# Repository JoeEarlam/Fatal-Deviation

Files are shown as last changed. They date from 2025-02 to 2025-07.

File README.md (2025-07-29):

# Fatal Deviation

Fatal Deviation is my 1.5KG beetleweight lifter, with independent 4WD and electronic stability control. The name comes from Ireland's first full-length martial arts movie of the same name, which can be found in its entirety on youtube for the morbidly curious.

This repository is not intended to be instructional - this isn't a full open-source project, but a reference for myself and others who want to see how the sausage is made. If you do build your own (or something similar), please let me know, I'd love to see more weird tiny beetleweights on the scene!

For more information on the design and build process, please check out my build thread: https://forum.bristolbotbuilders.com/t/fatal-deviation-my-over-engineered-beetleweight/232

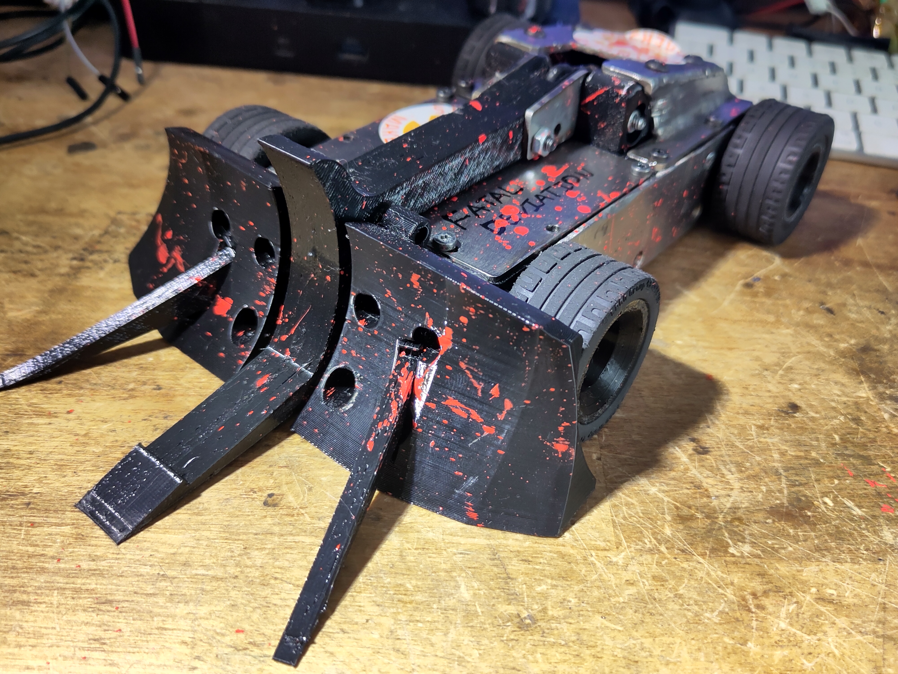
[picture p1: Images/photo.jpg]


TPU front end, the night before Bristol Bot Builders' Summer Showdown, July 2025



Steel front end, for Robodojo, May 2025

## Design Criteria and Overview

I impulse bought a TIG welder in Lidl and needed more excuses to use it. Somebody on the internet said that it wasn't possible to build a somewhat competitive beetleweight robot almost entirely from steel. Together, that was all the motivation I needed. Watching fast lifter/grappler bots like P1, Whiplash, Claw Viper/Red Storm, and having previous experience racing RC cars, I knew how I wanted the bot to drive - fast, agile, predictable. This gave me some design requirements:

* Extremely compact chassis to allow as much armour coverage as possible.
* Four independently controlled drive motors, for redundancy and torque vectoring.
* Small, compact and powerful lifter mechanism.
* As much RGB as possible while still having enough power left over for the bot to drive.

## Mechanical Design

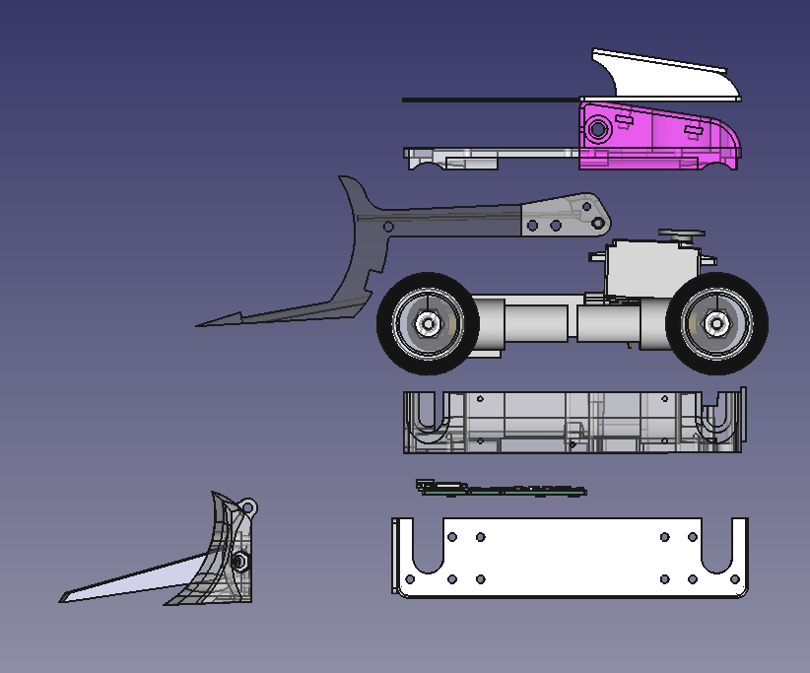
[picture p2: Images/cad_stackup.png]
CAD stackup


The mechanical design uses a welded 304 stainless steel chassis tub - 2mm sides and bottom, with 4mm front and rear sections. Stainless was chosen for aesthetic reasons, and because 2mm hardox is very difficult to source.

The wedge is soft-mounted via threaded aluminium inserts pressed into TPU brackets. The tub protects a TPU clamshell that sandwiches the internal components together, via long screws and threaded inserts to pull it together. Self-tapping screws are used to hold the clamshell into the chassis tub which suspends all the internal components and hopefully provides some shock absorption.

The TPU clamshell design means all the internal components of the robot can be removed as a unit for repair on the bench. Accessing any component only takes a couple of minutes, although unfortunately due to the compact design many connections have to be soldered rather than connectorised/

## Electronic Design

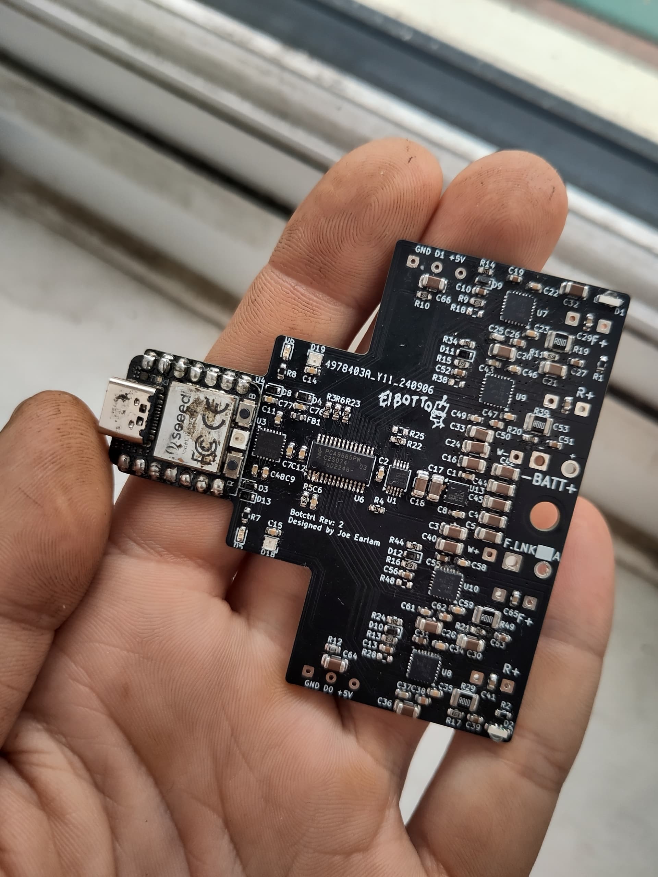
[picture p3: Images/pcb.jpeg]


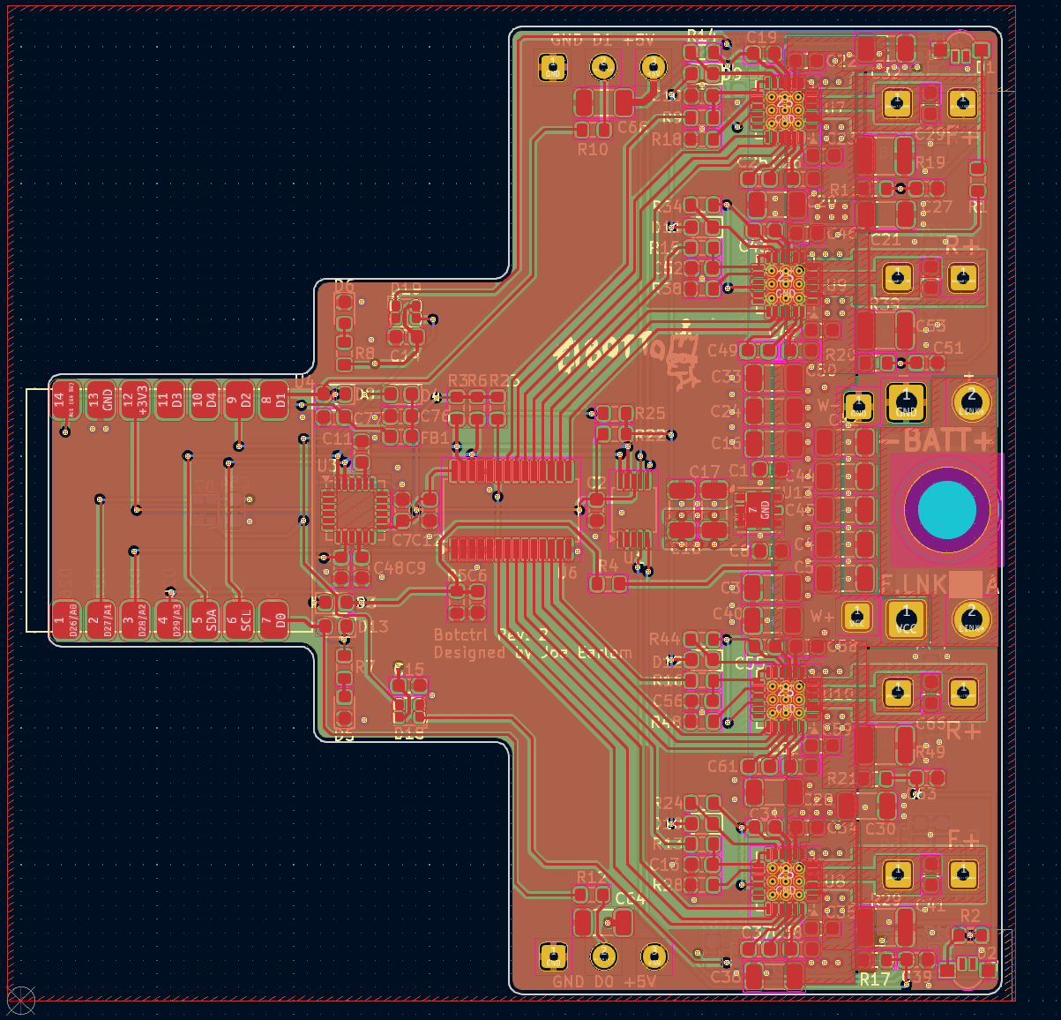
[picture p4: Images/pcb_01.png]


The only way to cram electronics into the remaining space inside the bot is to integrate every function (aside from the receiver) into a single PCB. In approximately 50x70mm total board area, the PCB provides:

* Seeed Xiao RP2040 microcontroller
* 4x 6A drive channels (TI DRV8256P drivers), with current sensing.
* MPU6050 gyro + accelerometer
* IBUS receiver compatible
* Servo power and signal pads
* 7x WS2812 RGB LEDs

The four layer PCB was designed with heavy usage of copper pours, optimised to keep resistance (both electrical and thermal) and inductance as low as possible when using cheap 1oz copper fabrication processes (2oz often costs 3-4 as much as 1oz!). The design also keeps the hot and EMI-prone motor drivers and servo power pads far away from the sensitive IMU and MCU. While only supposed to run 2-3 minutes at a time for events, it's been stress tested with 5-10 minutes of continuous running and barely rises over 45c, even with no airflow and four hot motors spinning inside the bot.

## Software Design

The software is written in Arduino IDE, utilising both cores of the RP2040 microcontroller. The firmware uses the wonderful [TaskScheduler](https://github.com/arkhipenko/TaskScheduler) library by arkhipenko to handle timing and looping, with modularity provided by custom classes containing motor driver logic, IMU data processing, and drive maths. The task-based asynchronous code allows predictable timing for data acquisition and filter functions, while also optimising for minimum latency by triggering drive maths routines the instant that a new radio packet is received.

IMU gyroscope data is used, in combination with the steering channel data received from the RC transmitter, as the input and target variables of a PID loop, which provides the electronic stability control - the bot will steer to self correct back to its intended course if disrupted; either by a bump in the floor or contact with another robot, and allows the bot to hold dead straight line acceleration or smooth drifts on low-friction surfaces where it would otherwise spin out uncontrollably. To improve the turning radius (which is otherwise somewhat poor due to the long aspect ratio of the bot) the front inside wheel is braked on sharp turns, while the rear inside wheel coasts, shifting the centre of rotation for the bot forwards.

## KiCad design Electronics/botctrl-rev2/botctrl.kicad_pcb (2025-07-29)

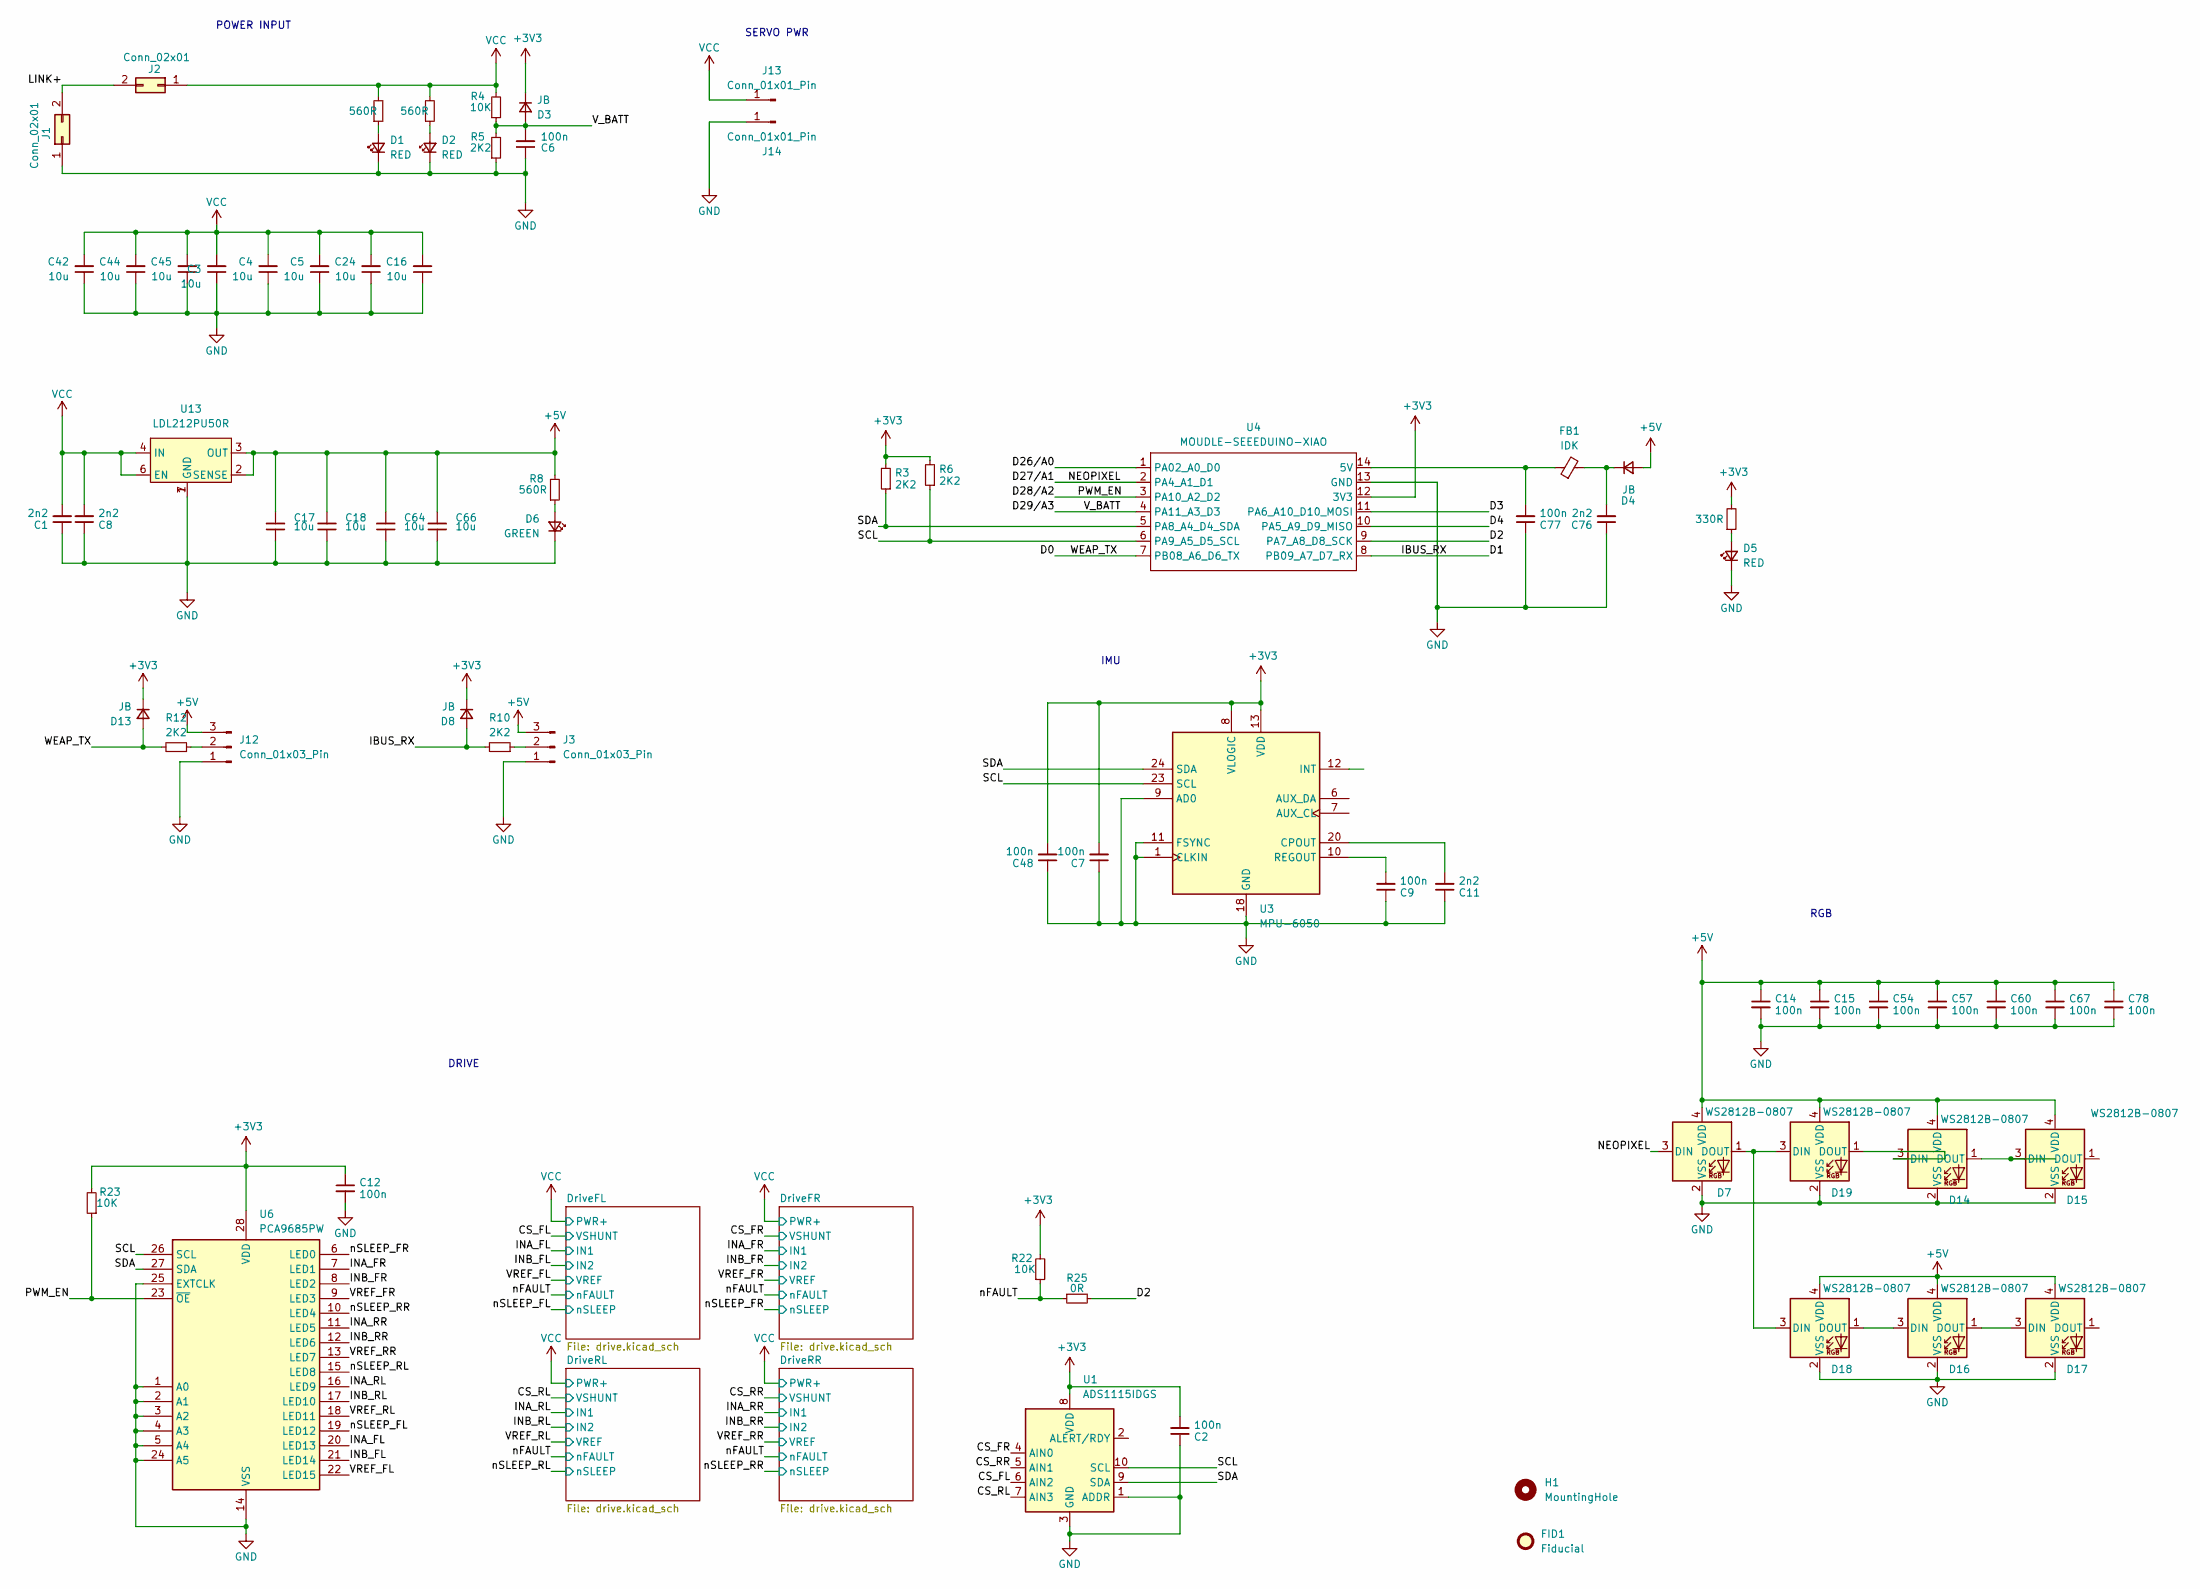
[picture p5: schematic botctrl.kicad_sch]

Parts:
C1, C8, C11, C76: 2n2; C_0603_1608Metric
C2, C6, C7, C9, C12, C14, C15, C48, C54, C57, C60, C67, C77, C78: 100n; C_0603_1608Metric
C3, C4, C5, C16, C17, C18, C24, C42, C44, C45, C64, C66: 10u; C_1206_3216Metric
D1, D2: RED; LED_Kingbright_APFA3010_3x1.5mm_Horizontal
D3, D4, D8, D13: JB; D_0603_1608Metric
D5: RED; D_0603_1608Metric
D6: GREEN; D_0603_1608Metric
D7, D14, D15, D16, D17, D18, D19: WS2812B-0807; WS2812-0807
FB1: IDK; L_0603_1608Metric; Part Number 0R
FID1: Fiducial; el-botto
H1: MountingHole; MountingHole_4.3mm_M4_DIN965
J1, J2: Conn_02x01; SolderWire-0.75sqmm_1x02_P4.8mm_D1.25mm_OD2.3mm
J3, J12: Conn_01x03_Pin; SolderWire-0.127sqmm_1x03_P3.7mm_D0.48mm_OD1mm
J13, J14: Conn_01x01_Pin; SolderWire-0.25sqmm_1x01_D0.65mm_OD1.7mm
R1, R2, R8: 560R; R_0603_1608Metric
R3, R5, R6, R10, R12: 2K2; R_0603_1608Metric
R4, R22, R23: 10K; R_0603_1608Metric
R7: 330R; R_0603_1608Metric
R25: 0R; R_0603_1608Metric
U1: ADS1115IDGS; TSSOP-10_3x3mm_P0.5mm
U3: MPU-6050; InvenSense_QFN-24_4x4mm_P0.5mm
U4: MOUDLE-SEEEDUINO-XIAO; MOUDLE14P-SMD-2.54-21X17.8MM
U6: PCA9685PW; TSSOP-28_4.4x9.7mm_P0.65mm
U13: LDL212PU50R; DFN-6-1EP_3x3mm_P0.95mm_EP1.7x2.6mm

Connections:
+3V3: C2.2, C7.2, C12.1, C48.2, D3.1 (K), D8.1 (K), D13.1 (K), R3.2, R6.2, R7.2, R22.2, R23.2, U1.8 (VDD), U3.8 (VLOGIC), U3.13 (VDD), U4.12 (3V3), U6.28 (VDD)
+5V: C14.1, C15.1, C17.2, C18.2, C54.1, C57.1, C60.1, C64.2, C66.2, C67.1, C78.1, D4.2 (A), D7.4 (VDD), D14.4 (VDD), D15.4 (VDD), D16.4 (VDD), D17.4 (VDD), D18.4 (VDD), D19.4 (VDD), J3.3, J12.3, R8.2, U13.2 (SENSE), U13.3 (OUT)
/CS_FL: U1.6 (AIN2); also elsewhere on the board
/CS_FR: U1.4 (AIN0); also elsewhere on the board
/CS_RL: U1.7 (AIN3); also elsewhere on the board
/CS_RR: U1.5 (AIN1); also elsewhere on the board
/D0: D13.2 (A), R12.2, U4.7 (PB08_A6_D6_TX)
/D1: D8.2 (A), R10.2, U4.8 (PB09_A7_D7_RX)
/D2: R25.2, U4.9 (PA7_A8_D8_SCK)
/D3: U4.11 (PA6_A10_D10_MOSI)
/D4: U4.10 (PA5_A9_D9_MISO)
/D26/A0: U4.1 (PA02_A0_D0)
/D27/A1: D7.3 (DIN), U4.2 (PA4_A1_D1)
/D28/A2: R23.1, U4.3 (PA10_A2_D2), U6.23 (~OE)
/D29/A3: C6.2, D3.2 (A), R4.1, R5.2, U4.4 (PA11_A3_D3)
/INA_FL: U6.20 (LED13); also elsewhere on the board
/INA_FR: U6.7 (LED1); also elsewhere on the board
/INA_RL: U6.16 (LED9); also elsewhere on the board
/INA_RR: U6.11 (LED5); also elsewhere on the board
/INB_FL: U6.21 (LED14); also elsewhere on the board
/INB_FR: U6.8 (LED2); also elsewhere on the board
/INB_RL: U6.17 (LED10); also elsewhere on the board
/INB_RR: U6.12 (LED6); also elsewhere on the board
/LINK+: J1.2, J2.2
/SCL: R6.1, U1.10 (SCL), U3.23 (SCL), U4.6 (PA9_A5_D5_SCL), U6.26 (SCL)
/SDA: R3.1, U1.9 (SDA), U3.24 (SDA), U4.5 (PA8_A4_D4_SDA), U6.27 (SDA)
/VREF_FL: U6.22 (LED15); also elsewhere on the board
/VREF_FR: U6.9 (LED3); also elsewhere on the board
/VREF_RL: U6.18 (LED11); also elsewhere on the board
/VREF_RR: U6.13 (LED7); also elsewhere on the board
/nFAULT: R22.1, R25.1; also elsewhere on the board
/nSLEEP_FL: U6.19 (LED12); also elsewhere on the board
/nSLEEP_FR: U6.6 (LED0); also elsewhere on the board
/nSLEEP_RL: U6.15 (LED8); also elsewhere on the board
/nSLEEP_RR: U6.10 (LED4); also elsewhere on the board
GND: C1.1, C2.1, C3.1, C4.1, C5.1, C6.1, C7.1, C8.1, C9.1, C11.1, C12.2, C14.2, C15.2, C16.1, C17.1, C18.1, C24.1, C42.1, C44.1, C45.1, C48.1, C54.2, C57.2, C60.2, C64.1, C66.1, C67.2, C76.1, C77.1, C78.2, D1.1 (K), D2.1 (K), D5.1 (K), D6.1 (K), D7.2 (VSS), D14.2 (VSS), D15.2 (VSS), D16.2 (VSS), D17.2 (VSS), D18.2 (VSS), D19.2 (VSS), J1.1, J3.1, J12.1, J14.1, R5.1, U1.1 (ADDR), U1.3 (GND), U3.1 (CLKIN), U3.9 (AD0), U3.11 (FSYNC), U3.18 (GND), U4.13 (GND), U6.1 (A0), U6.2 (A1), U6.3 (A2), U6.4 (A3), U6.5 (A4), U6.14 (VSS), U6.24 (A5), U6.25 (EXTCLK), U13.1 (GND), U13.7 (GND); also elsewhere on the board
unnamed: D1.2 (A), R1.1
unnamed: D2.2 (A), R2.1
unnamed: C76.2, D4.1 (K), FB1.2
unnamed: D5.2 (A), R7.1
unnamed: D6.2 (A), R8.1
unnamed: D14.3 (DIN), D19.1 (DOUT)
unnamed: D14.1 (DOUT), D15.3 (DIN)
unnamed: D16.3 (DIN), D18.1 (DOUT)
unnamed: D16.1 (DOUT), D17.3 (DIN)
unnamed: D7.1 (DOUT), D18.3 (DIN), D19.3 (DIN)
unnamed: J3.2, R10.1
unnamed: J12.2, R12.1
unnamed: C11.2, U3.20 (CPOUT)
unnamed: C9.2, U3.10 (REGOUT)
unnamed: C77.2, FB1.1, U4.14 (5V)
VCC: C1.2, C3.2, C4.2, C5.2, C8.2, C16.2, C24.2, C42.2, C44.2, C45.2, J2.1, J13.1, R1.2, R2.2, R4.2, U13.4 (IN), U13.6 (EN); also elsewhere on the board

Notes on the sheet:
DRIVE
POWER INPUT
SERVO PWR
IMU
RGB

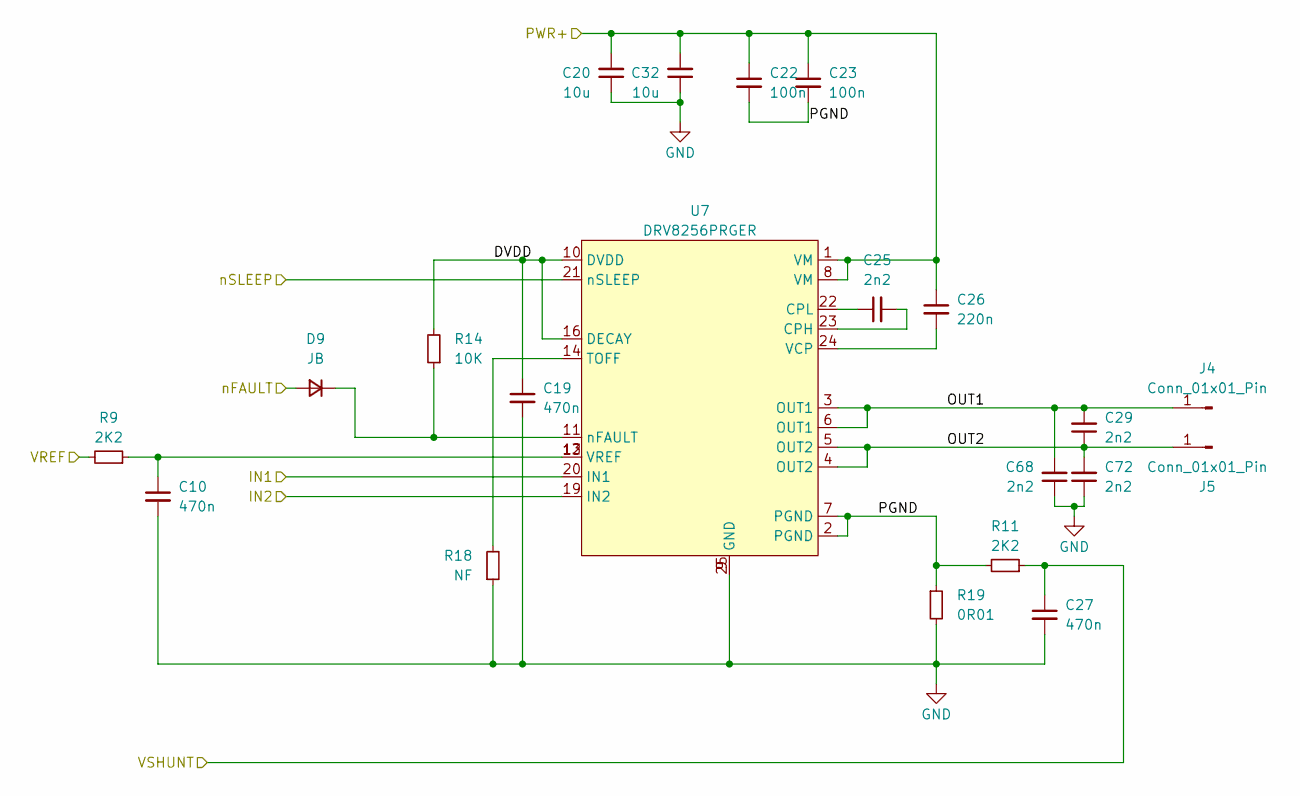
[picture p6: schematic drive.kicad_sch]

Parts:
C10, C19, C27: 470n; C_0603_1608Metric
C20, C32: 10u; C_1206_3216Metric
C22, C23: 100n; C_0603_1608Metric
C25, C29, C68, C72: 2n2; C_0603_1608Metric
C26: 220n; C_0603_1608Metric
D9: JB; D_0603_1608Metric
J4, J5: Conn_01x01_Pin; SolderWire-0.25sqmm_1x01_D0.65mm_OD1.7mm
R9, R11: 2K2; R_0603_1608Metric
R14: 10K; R_0603_1608Metric
R18: NF; R_0603_1608Metric
R19: 0R01; R_1210_3225Metric
U7: DRV8256PRGER; VQFN-24-1EP_4x4mm_P0.5mm_EP2.45x2.45mm_ThermalVias

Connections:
/CS_FL: C27.1, R11.1; also elsewhere on the board
/DriveFL/DVDD: C19.1, R14.2, U7.10 (DVDD), U7.16 (DECAY)
/DriveFL/OUT1: C29.2, C68.2, J4.1, U7.3 (OUT1), U7.6 (OUT1)
/DriveFL/OUT2: C29.1, C72.2, J5.1, U7.4 (OUT2), U7.5 (OUT2)
/DriveFL/PGND: C22.2, C23.2, R11.2, R19.1, U7.2 (PGND), U7.7 (PGND)
/INA_FL: U7.20 (IN1); also elsewhere on the board
/INB_FL: U7.19 (IN2); also elsewhere on the board
/VREF_FL: R9.2; also elsewhere on the board
/nFAULT: D9.2 (A); also elsewhere on the board
/nSLEEP_FL: U7.21 (nSLEEP); also elsewhere on the board
GND: C10.2, C19.2, C20.1, C27.2, C32.1, C68.1, C72.1, R18.1, R19.2, U7.9 (GND), U7.25 (GND); also elsewhere on the board
unnamed: C10.1, R9.1, U7.12 (VREF), U7.13 (VREF)
unnamed: D9.1 (K), R14.1, U7.11 (nFAULT)
unnamed: C25.2, U7.23 (CPH)
unnamed: C25.1, U7.22 (CPL)
unnamed: R18.2, U7.14 (TOFF)
unnamed: C26.2, U7.24 (VCP)
VCC: C20.2, C22.1, C23.1, C26.1, C32.2, U7.1 (VM), U7.8 (VM); also elsewhere on the board

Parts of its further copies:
C13, C31, C39, C43, C51, C52, C55, C56, C63: 470n; C_0603_1608Metric
C21, C28, C30, C33, C36, C40: 10u; C_1206_3216Metric
C34, C35, C46, C47, C58, C59: 100n; C_0603_1608Metric
C37, C41, C49, C53, C61, C65, C69, C70, C71, C73, C74, C75: 2n2; C_0603_1608Metric
C38, C50, C62: 220n; C_0603_1608Metric
D10, D11, D12: JB; D_0603_1608Metric
J6, J7, J8, J9, J10, J11: Conn_01x01_Pin; SolderWire-0.25sqmm_1x01_D0.65mm_OD1.7mm
R13, R15, R16, R17, R20, R21: 2K2; R_0603_1608Metric
R24, R34, R44: 10K; R_0603_1608Metric
R28, R38, R48: NF; R_0603_1608Metric
R29, R39, R49: 0R01; R_1210_3225Metric
U8, U9, U10: DRV8256PRGER; VQFN-24-1EP_4x4mm_P0.5mm_EP2.45x2.45mm_ThermalVias

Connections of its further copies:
/CS_FR: C39.1, R17.1; also elsewhere on the board
/CS_RL: C51.1, R20.1; also elsewhere on the board
/CS_RR: C63.1, R21.1; also elsewhere on the board
/DriveFR/DVDD: C31.1, R24.2, U8.10 (DVDD), U8.16 (DECAY)
/DriveFR/OUT1: C41.2, C69.2, J6.1, U8.3 (OUT1), U8.6 (OUT1)
/DriveFR/OUT2: C41.1, C73.2, J7.1, U8.4 (OUT2), U8.5 (OUT2)
/DriveFR/PGND: C34.2, C35.2, R17.2, R29.1, U8.2 (PGND), U8.7 (PGND)
/DriveRL/DVDD: C43.1, R34.2, U9.10 (DVDD), U9.16 (DECAY)
/DriveRL/OUT1: C53.2, C70.2, J8.1, U9.3 (OUT1), U9.6 (OUT1)
/DriveRL/OUT2: C53.1, C74.2, J9.1, U9.4 (OUT2), U9.5 (OUT2)
/DriveRL/PGND: C46.2, C47.2, R20.2, R39.1, U9.2 (PGND), U9.7 (PGND)
/DriveRR/DVDD: C55.1, R44.2, U10.10 (DVDD), U10.16 (DECAY)
/DriveRR/OUT1: C65.2, C71.2, J10.1, U10.3 (OUT1), U10.6 (OUT1)
/DriveRR/OUT2: C65.1, C75.2, J11.1, U10.4 (OUT2), U10.5 (OUT2)
/DriveRR/PGND: C58.2, C59.2, R21.2, R49.1, U10.2 (PGND), U10.7 (PGND)
/INA_FR: U8.20 (IN1); also elsewhere on the board
/INA_RL: U9.20 (IN1); also elsewhere on the board
/INA_RR: U10.20 (IN1); also elsewhere on the board
/INB_FR: U8.19 (IN2); also elsewhere on the board
/INB_RL: U9.19 (IN2); also elsewhere on the board
/INB_RR: U10.19 (IN2); also elsewhere on the board
/VREF_FR: R13.2; also elsewhere on the board
/VREF_RL: R15.2; also elsewhere on the board
/VREF_RR: R16.2; also elsewhere on the board
/nFAULT: D10.2 (A), D11.2 (A), D12.2 (A); also elsewhere on the board
/nSLEEP_FR: U8.21 (nSLEEP); also elsewhere on the board
/nSLEEP_RL: U9.21 (nSLEEP); also elsewhere on the board
/nSLEEP_RR: U10.21 (nSLEEP); also elsewhere on the board
GND: C13.2, C21.1, C28.1, C30.1, C31.2, C33.1, C36.1, C39.2, C40.1, C43.2, C51.2, C52.2, C55.2, C56.2, C63.2, C69.1, C70.1, C71.1, C73.1, C74.1, C75.1, R28.1, R29.2, R38.1, R39.2, R48.1, R49.2, U8.9 (GND), U8.25 (GND), U9.9 (GND), U9.25 (GND), U10.9 (GND), U10.25 (GND); also elsewhere on the board
unnamed: C13.1, R13.1, U8.12 (VREF), U8.13 (VREF)
unnamed: C52.1, R15.1, U9.12 (VREF), U9.13 (VREF)
unnamed: C56.1, R16.1, U10.12 (VREF), U10.13 (VREF)
unnamed: D10.1 (K), R24.1, U8.11 (nFAULT)
unnamed: D11.1 (K), R34.1, U9.11 (nFAULT)
unnamed: D12.1 (K), R44.1, U10.11 (nFAULT)
unnamed: C37.2, U8.23 (CPH)
unnamed: C37.1, U8.22 (CPL)
unnamed: R28.2, U8.14 (TOFF)
unnamed: C38.2, U8.24 (VCP)
unnamed: C49.2, U9.23 (CPH)
unnamed: C49.1, U9.22 (CPL)
unnamed: R38.2, U9.14 (TOFF)
unnamed: C50.2, U9.24 (VCP)
unnamed: C61.2, U10.23 (CPH)
unnamed: C61.1, U10.22 (CPL)
unnamed: R48.2, U10.14 (TOFF)
unnamed: C62.2, U10.24 (VCP)
VCC: C21.2, C28.2, C30.2, C33.2, C34.1, C35.1, C36.2, C38.1, C40.2, C46.1, C47.1, C50.1, C58.1, C59.1, C62.1, U8.1 (VM), U8.8 (VM), U9.1 (VM), U9.8 (VM), U10.1 (VM), U10.8 (VM); also elsewhere on the board

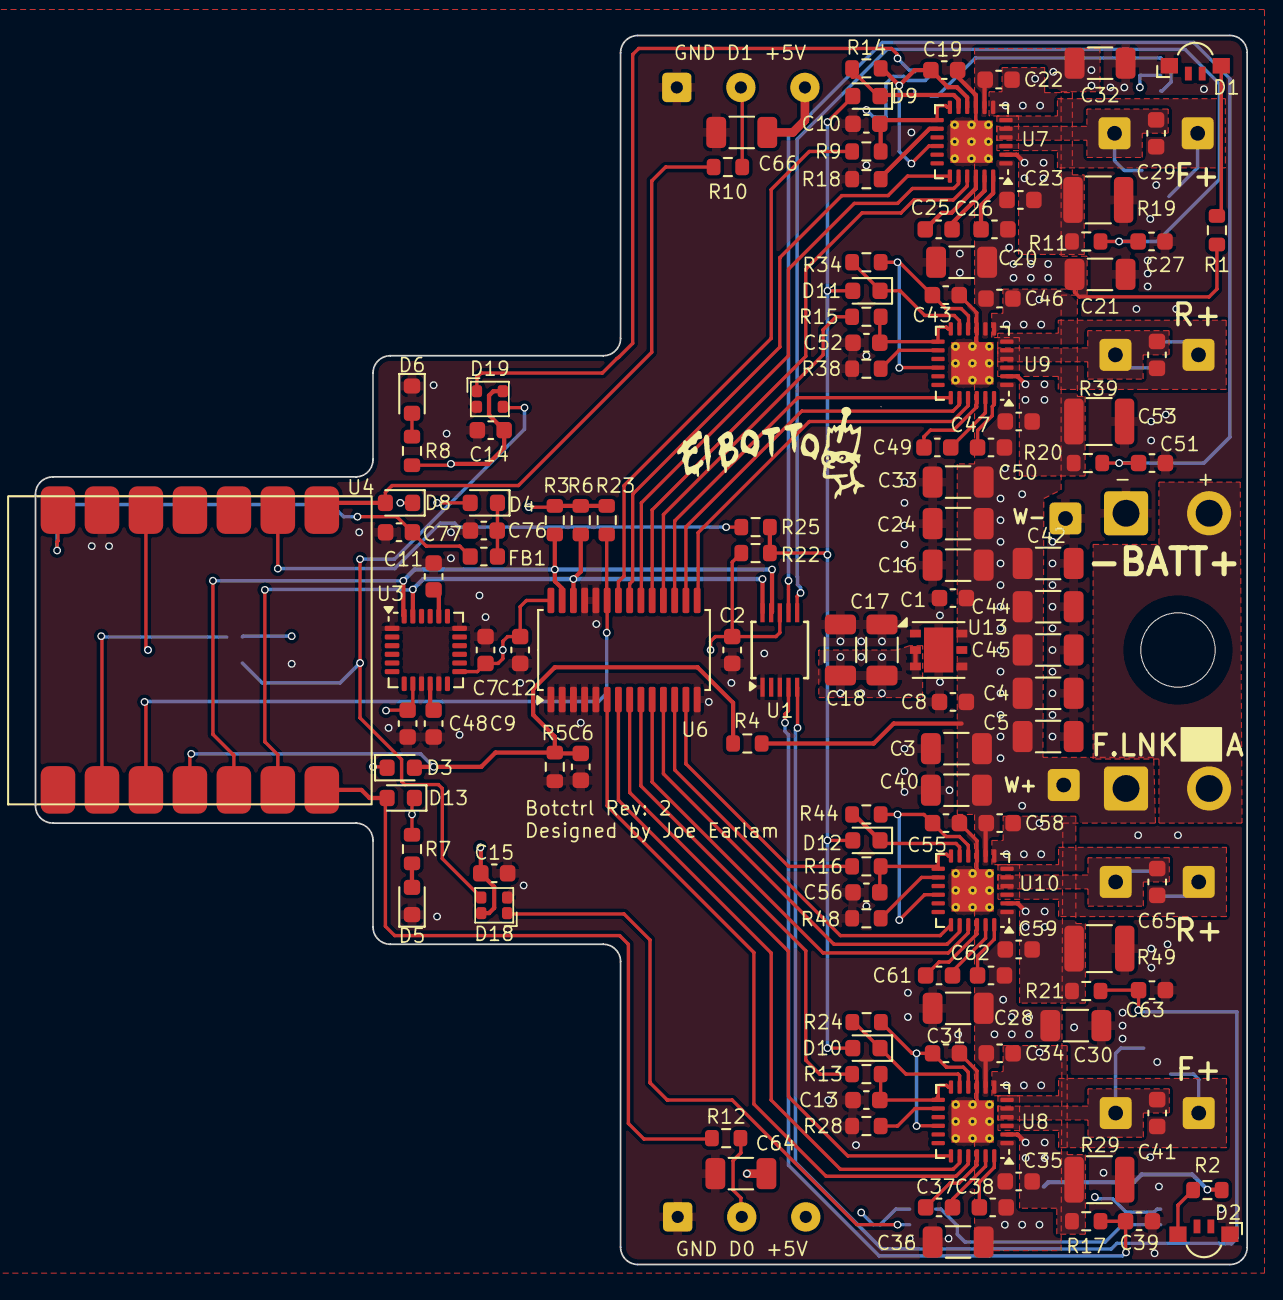
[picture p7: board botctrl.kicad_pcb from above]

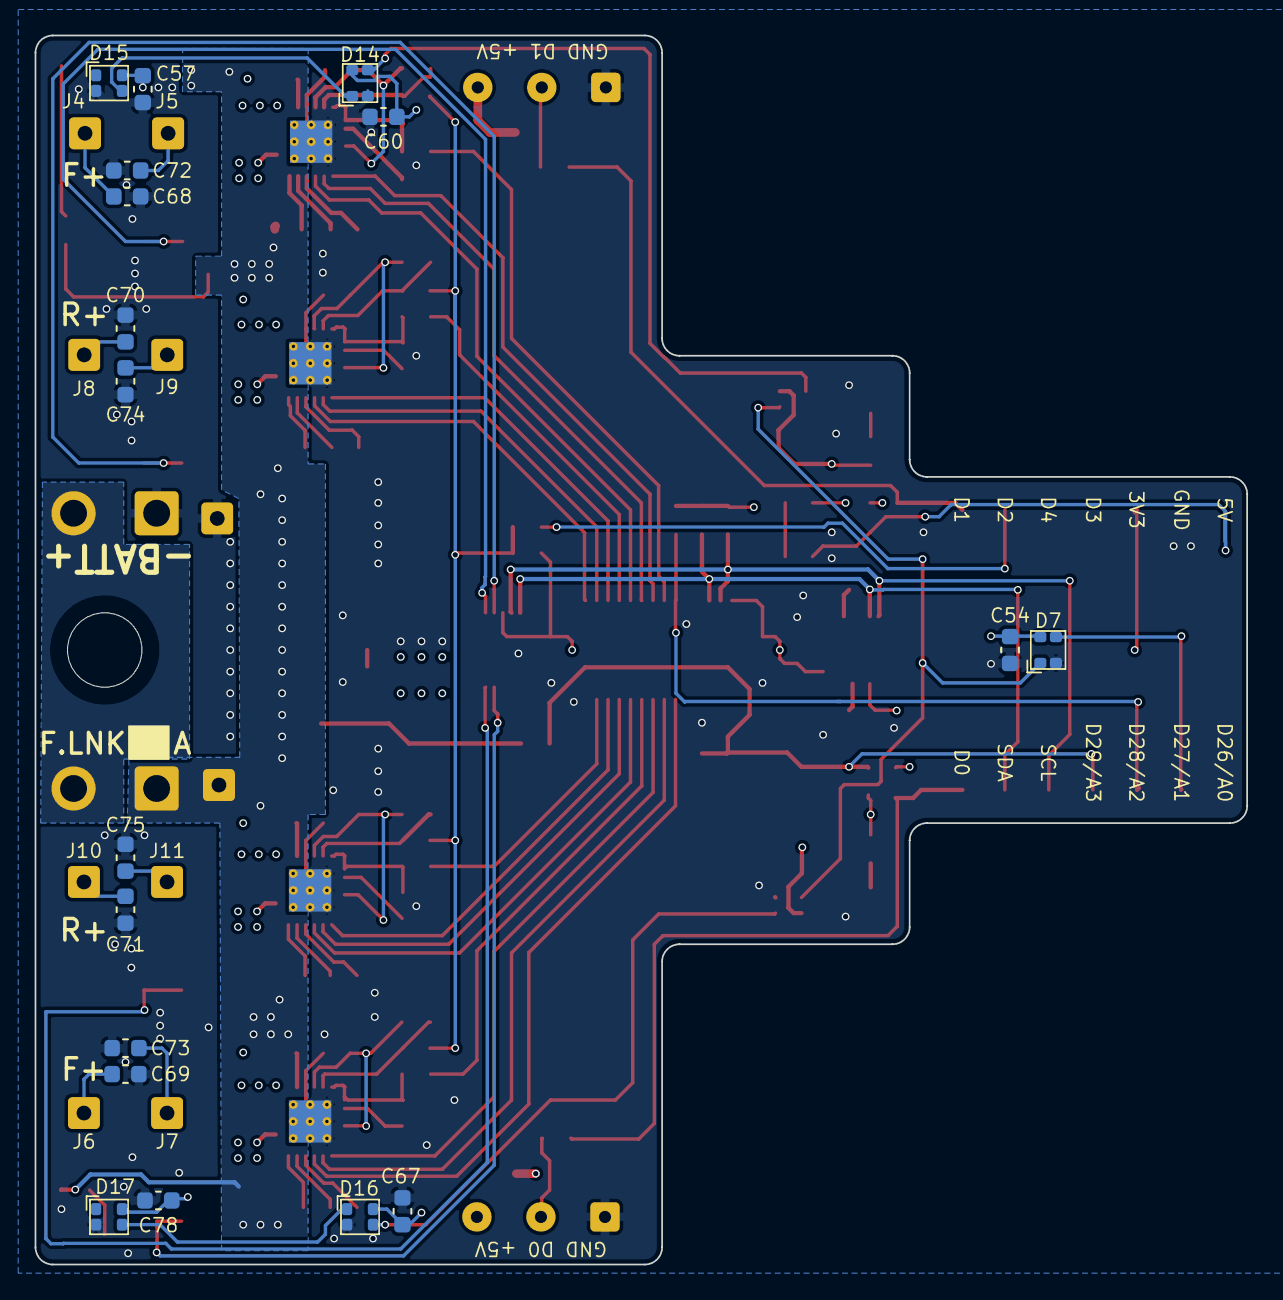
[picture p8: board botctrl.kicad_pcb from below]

Board: 4 copper layers, 70.0 x 71.0 mm, 156 parts (18 on the bottom side), 89 nets.

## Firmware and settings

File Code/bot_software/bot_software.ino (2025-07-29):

#include "src/bot_software.h"

#include <Wire.h>
#include <Adafruit_NeoPixel.h>
#include <Adafruit_ADS1X15.h>
#include <TaskScheduler.h>
#include <Servo.h>

#include "src/motor.h"
#include "src/drive.h"
#include "src/IMU.h"
#include "src/serialbuf.h"

Adafruit_NeoPixel stripB(LED_COUNT, PIN_NEO_BRD, NEO_RGB + NEO_KHZ800);
Adafruit_NeoPixel stripX(1, PIN_NEO_XIAO, NEO_GRB + NEO_KHZ800);
Adafruit_PWMServoDriver pwm = Adafruit_PWMServoDriver();
Adafruit_ADS1015 ads;

Motor FL(pwm, INA_FL, INB_FL, VREF_FL, NSLEEP_FL);
Motor FR(pwm, INA_FR, INB_FR, VREF_FR, NSLEEP_FR);
Motor RL(pwm, INA_RL, INB_RL, VREF_RL, NSLEEP_RL);
Motor RR(pwm, INA_RR, INB_RR, VREF_RR, NSLEEP_RR);

BotDrive drive;
BotMotion motion;
FlySkyIBus iBus;
Servo weaponOut;
SerialBuf serialBuf(Serial);

Scheduler ts0;
Scheduler ts1;

//core0
Task readRadio(0, TASK_FOREVER, &readRadioCB, &ts0);
Task mainTask(0, TASK_ONCE, &mainTaskCB, &ts0);
Task readAnalogue(IBUS_PERIOD * 4, TASK_FOREVER, &readAnalogueCB, &ts0);
Task readImu(IBUS_PERIOD, TASK_FOREVER, &readImuCB, &ts0);
Task writePWM(0, TASK_ONCE, &writePWMCB, &ts0);

//core1
Task inputHandler(0, TASK_ONCE, &inputHandlerCB, &ts1);
Task weaponHandler(0, TASK_ONCE, &weaponCB, &ts1);
Task rgb(10, TASK_FOREVER, &rgbCB, &ts1);
Task debugSerial(0, TASK_FOREVER, &debugSerialCB, &ts1);

Radio_t rxFrame;
Drive_t driveVals;
IMU_t imuData;
Pwr_t pwrData;

RadioState_t radioState;
BotState_t botState;
BattState_t battState;

void setup() {
  rp2040.idleOtherCore();

  Serial.begin();
  setupiBus();
  setupInputs();
  setupOutputs();
  setupDrive();
  motion.begin();
  setupADC();
  setupRGB();

  if (watchdog_enable_caused_reboot()) {
    botState = BOT_NOT_OK;
  }

  ts0.enableAll();
  ts1.enableAll();

  rp2040.wdt_begin(500);
  rp2040.resumeOtherCore();
}

void setup1() {
  delayMicroseconds(100);
}

void readRadioCB() {
  static uint32_t lastRadioTime;
  uint16_t chanData[IBUS_CHANNELS];

  iBus.loop();

  if (iBus.readChannels(chanData)) {
    lastRadioTime = millis();
    radioState = RADIO_OK;
    rxFrame = parseChannels(chanData);
    mainTask.restart();
  }

  if (millis() > (lastRadioTime + 100)) {
    lastRadioTime = millis();
    radioState = RADIO_DC;
    rxFrame = { 0 };
    mainTask.restart();
  }
}

void mainTaskCB() {
  if (radioState == RADIO_DC) {
    rxFrame = { 0 };
    drive.setInputs(rxFrame);
    drive.doMaths();
    writePWM.restart();
  } else {
    inputHandler.restart();
    drive.setIMU(imuData);
    drive.setInputs(rxFrame);
    drive.doMaths();
    writePWM.restart();
  }

  Msg_t msg;
  sprintf(msg.txt, "S:%d T:%d FL:%d FR:%d GY:", rxFrame.steering, rxFrame.throttle, driveVals.FL.duty, driveVals.FR.duty);
  Serial.println(imuData.g.z);
  serialBuf.pushMsg(msg);
}

void inputHandlerCB() {
  static bool lastButtVal;
  static int16_t lastSwVal;

  if (rxFrame.button != lastButtVal) {
    lastButtVal = rxFrame.button;
    weaponOut.writeMicroseconds(WEAPON_UP);
    weaponHandler.restartDelayed(500);
  }

  if (rxFrame.toggle != lastSwVal) {
    lastSwVal = rxFrame.toggle;
    weaponHandler.restart();
  }
}

void weaponCB() {
  weaponOut.writeMicroseconds(rxFrame.toggle);
}

void writePWMCB() {
  driveVals = drive.getDrive();

  FL.setMotor(driveVals.FL);
  FR.setMotor(driveVals.FR);
  RL.setMotor(driveVals.RL);
  RR.setMotor(driveVals.RR);

  rp2040.wdt_reset();
}

void debugSerialCB() {
  serialBuf.sendBuffer();
}

void readImuCB() {
  motion.update();
  imuData = motion.getIMU();
}

void readAnalogueCB() {
  pwrData = readPowerData();
}

void rgbCB() {
  if (radioState == RADIO_DC) {
    fillRGB(0, 0, 255);
  } else {
    if (battState == BATT_OK) {
      fillRainbow();
    } else if (botState == BOT_NOT_OK) {
      fillRGB(127, 127, 0);
    } else {
      fillRGB(255, 0, 0);
    }
  }
}

void fillRainbow() {
  static uint16_t hue;
  static uint32_t lastMillis;
  uint32_t currentMillis = millis();

  hue = hue + (currentMillis - lastMillis) * RGB_SPEED;

  stripB.rainbow(hue);
  stripX.rainbow(hue);
  stripX.show();
  stripB.show();

  lastMillis = currentMillis;
}

void fillRGB(uint8_t r, uint8_t g, uint8_t b) {
  stripB.fill(stripB.Color(r, g, b));
  stripX.fill(stripX.Color(g, r, b));
  stripB.show();
  stripX.show();
}

Radio_t parseChannels(uint16_t (&chanData)[IBUS_CHANNELS]) {
  Radio_t thisFrame;

  thisFrame.steering = map(chanData[0], 1050, 1950, MAX_PWM, -MAX_PWM);
  thisFrame.throttle = map(chanData[1], 1050, 1950, -MAX_PWM, MAX_PWM);
  thisFrame.button = map(chanData[2], 1000, 2000, 0, 1);
  thisFrame.toggle = chanData[3];
  thisFrame.knobL = map(chanData[4], 1000, 2000, 0, 100);
  thisFrame.knobR = map(chanData[5], 1000, 2000, 10, 200);

  return thisFrame;
}

//10mR shunt
//10mV/A
Pwr_t readPowerData() {
  Pwr_t pwr;

  pwr.v = readBattVolts();
  battState = getBattState();

  pwr.iFL = ads.computeVolts(ads.readADC_SingleEnded(0)) * 100;
  pwr.iFR = ads.computeVolts(ads.readADC_SingleEnded(2)) * 100;
  pwr.iRL = ads.computeVolts(ads.readADC_SingleEnded(1)) * 100;
  pwr.iRR = ads.computeVolts(ads.readADC_SingleEnded(3)) * 100;

  return pwr;
}

BattState_t getBattState() {
  float lowBattRst = LOW_BATT_VOLTS + 0.2;
  static bool lowBattEvent;

  if (pwrData.v < LOW_BATT_VOLTS) {
    lowBattEvent = true;
  }
  if (pwrData.v > lowBattRst) {
    lowBattEvent = false;
  }

  if (lowBattEvent) {
    return BATT_LOW;
  } else {
    return BATT_OK;
  }
}

//10K/2K2 voltage divider
//10V = 1.803V @ ADC
float readBattVolts() {
  float adc = analogRead(PIN_V_BATT);

  const float vRef = 3.3;
  const uint16_t fsr = 1023;

  adc = adc * (vRef / fsr);

  return adc * 5.57;  //(10/1.803v)+0.02 for calibration
}


void loop() {
  ts0.execute();
}

void loop1() {
  ts1.execute();
}

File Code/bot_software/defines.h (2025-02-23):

#ifndef DEFINES_H
#define DEFINES_H

//pins
#define PIN_WEAP 0
#define PIN_IBUS 1
#define PIN_DRV_FAULT 2
#define PIN_NEO_BRD 27
#define PIN_NEO_PWR 11
#define PIN_NEO_XIAO 12
#define PIN_PWM_EN 28
#define PIN_V_BATT A3

//PWM output channels
#define NSLEEP_FL 0
#define INA_FL 1
#define INB_FL 2
#define VREF_FL 3

#define NSLEEP_RL 4
#define INA_RL 5
#define INB_RL 6
#define VREF_RL 7

#define NSLEEP_RR 8
#define INA_RR 10
#define INB_RR 9
#define VREF_RR 11

#define NSLEEP_FR 12
#define INA_FR 14
#define INB_FR 13
#define VREF_FR 15

//misc
#define LED_COUNT 4
#define RGB_SPEED 16
#define IBUS_PERIOD 7
#define LOW_BATT_VOLTS 9.5

#endif

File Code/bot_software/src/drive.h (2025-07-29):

#ifndef DRIVE_H
#define DRIVE_H

#include "defines.h"
#include "types.h"
#include "motor.h"
#include "IMU.h"
#include <PID_v1.h>


struct Drive_t {
  MotorPWM_t FL, FR, RL, RR;
};

enum DriveState_t {
  IDLE,
  STATIONARY,
  MOVING,
};

enum DriveMode_t {
  TANK_OPENLOOP,
  TANK_CLOSEDLOOP,
  COMPUTE,
};

class BotDrive {
public:

  BotDrive();
  void begin();
  void setInputs(Radio_t inputs);
  void setIMU(IMU_t imuData);
  void setTunings(float p, float i);

  uint32_t doMaths();

  void setDriveAlgo(uint8_t algo);

  Drive_t getDrive();

private:
  DriveMode_t _driveMode = TANK_CLOSEDLOOP;
  DriveState_t _driveState;

  const uint16_t _deadZoneMov = MAX_PWM / 32;
  const uint16_t _deadZoneStat = MAX_PWM / 8;

  uint16_t _deadZoneThrot = _deadZoneMov;
  uint16_t _deadZoneSteer = _deadZoneStat;

  const float _maxGyroRads = 30;  //rate @ full send in rad/s

  Drive_t _driveData;
  IMU_t _imuData;

  int16_t _throttle;
  int16_t _steering;

  uint8_t _algoType;
  bool _enablePID = true;
  bool _enableExpThrot = true;

  double _PIDtgtRads, _PIDcurrRads, _PIDoutput;
  double _PID_Kp = 1, _PID_Ki = 0, _PID_Kd = 0;
  PID *_PID;

  int16_t _deadZoneInput(int16_t input, int16_t dz);
  float _runPID(float input);

  Drive_t _tankDrive(int16_t t, int16_t s);
  Drive_t _notForward(int16_t t, int16_t s);

  int16_t _expFunction(int16_t input, int16_t exp);
  float _steerToRads(float input);
  int16_t _radsToSteer(float input);
};

BotDrive::BotDrive() {
  _PID = new PID(&_PIDcurrRads, &_PIDoutput, &_PIDtgtRads, _PID_Kp, _PID_Ki, _PID_Kd, DIRECT);
}

void BotDrive::begin() {
  _PID->SetSampleTime(IBUS_PERIOD);
  _PID->SetOutputLimits(-_maxGyroRads, _maxGyroRads);
  _PID->SetMode(AUTOMATIC);
}

uint32_t BotDrive::doMaths() {
  uint32_t startTime = micros();

  int16_t t = _throttle;
  int16_t s = _steering;

  if (_enableExpThrot) t = _expFunction(t, 2);

  if (_driveState == IDLE) {
    _driveData.FL.coast = true;
    _driveData.FR.coast = true;
    _driveData.RL.coast = true;
    _driveData.RR.coast = true;
  } else {
    float pidOutRads;

    switch (_driveMode) {
      case TANK_OPENLOOP:
        _driveData = _tankDrive(t, s);
        break;
      case TANK_CLOSEDLOOP:
        pidOutRads = _runPID(_steerToRads(s));
        if (_enablePID && (_driveState == MOVING)) s = _radsToSteer(pidOutRads);

        _driveData = _tankDrive(t, s);
        break;
      case COMPUTE:
        _driveData = _tankDrive(t, s);  //bronk
        break;
    }
  }

  return startTime - micros();
}

float BotDrive::_runPID(float input) {
  _PIDtgtRads = input;
  _PIDcurrRads = _imuData.g.z;

  _PID->Compute();

  return _PIDoutput;
}



Drive_t BotDrive::_tankDrive(int16_t t, int16_t s) {
  Drive_t out;

  if (t > 0) {
    out.FL.duty = -s + t;
    out.FR.duty = s + t;

    out.FL.duty = constrain(out.FL.duty, -MAX_PWM, MAX_PWM);
    out.FR.duty = constrain(out.FR.duty, -MAX_PWM, MAX_PWM);

    if (out.FL.duty < 0) out.FL.duty = 0;
    else if (out.FL.duty <= (MAX_PWM / 8) && (out.FR.duty > MAX_PWM / 2)) {
      out.RL.duty = out.FR.duty / 8;
    } else {
      out.RL = out.FL;
    }

    if (out.FR.duty < 0) out.FR.duty = 0;
    else if (out.FR.duty <= (MAX_PWM / 8) && (out.FL.duty > MAX_PWM / 2)) {
      out.RR.duty = out.RL.duty / 8;
    } else {
      out.RR = out.FR;
    }

  } else {
    out = _notForward(t, s);
  }

  return out;
}

Drive_t BotDrive::_notForward(int16_t t, int16_t s) {
  Drive_t out;

  if (t > 0) {
    out.FL.duty = 0;
    out.FR.duty = 0;
    out.RL.duty = 0;
    out.RR.duty = 0;
  } else if (t < 0) {
    out.FL.duty = s + t;
    out.FR.duty = -s + t;

    out.FL.duty = constrain(out.FL.duty, -MAX_PWM, MAX_PWM);
    out.FR.duty = constrain(out.FR.duty, -MAX_PWM, MAX_PWM);

    if (out.FL.duty > 0) out.FL.duty = 0;
    if (out.FR.duty > 0) out.FR.duty = 0;

    out.RL = out.FL;
    out.RR = out.FR;

  } else {
    out.FL.duty = -s;
    out.FR.duty = s;
    out.FL.duty = constrain(out.FL.duty, -MAX_PWM, MAX_PWM);
    out.FR.duty = constrain(out.FR.duty, -MAX_PWM, MAX_PWM);
    out.RL = out.FL;
    out.RR = out.FR;
  }

  return out;
}


int16_t BotDrive::_expFunction(int16_t input, int16_t exp) {
  int32_t output = pow(input, exp) / pow(MAX_PWM + 1, exp - 1);

  if (output > (MAX_PWM - (MAX_PWM / 64))) output = MAX_PWM;
  if (output < (-MAX_PWM + (MAX_PWM / 64))) output = -MAX_PWM;

  if ((exp % 2 == 0) && (input < 0)) return int16_t(-output);
  else return int16_t(output);
}

float BotDrive::_steerToRads(float input) {
  const float scale = MAX_PWM / _maxGyroRads;
  float output = input / scale;

  return output;
}

int16_t BotDrive::_radsToSteer(float input) {
  const float scale = MAX_PWM / _maxGyroRads;
  float output = input * scale;

  return output;
}

void BotDrive::setInputs(Radio_t inputs) {
  static uint32_t lastActiveTime;
  _steering = _deadZoneInput(inputs.steering, _deadZoneSteer);
  _throttle = _deadZoneInput(inputs.throttle, _deadZoneThrot);

  if ((_steering != 0) || (_throttle != 0)) {
    lastActiveTime = millis();
    _deadZoneSteer = _deadZoneMov;
    _driveState = MOVING;
  }

  if ((_steering == 0) && (_throttle == 0)) {
    _driveState = STATIONARY;
  }

  if (millis() > lastActiveTime + 2000) {
    _deadZoneSteer = _deadZoneStat;
    _driveState = IDLE;
  }
}

int16_t BotDrive::_deadZoneInput(int16_t input, int16_t dz) {
  input = constrain(input, -MAX_PWM, MAX_PWM);

  if (dz == 0) return input;
  else {
    if (abs(input) < dz) {
      return 0;
    } else {
      int16_t scaledOutput = map(abs(input), dz, MAX_PWM, 0, MAX_PWM);
      if (input > 0) input = scaledOutput;
      if (input < 0) input = -scaledOutput;
      return input;
    }
  }
}

void BotDrive::setTunings(float p, float i) {
  _PID_Kp = p;
  _PID_Ki = i;

  if (_PID_Kp < 0) _PID_Kp = 0.1;
  if (_PID_Ki < 0) _PID_Ki = 0;
  _PID->SetTunings(_PID_Kp, _PID_Ki, _PID_Kd);
}

void BotDrive::setDriveAlgo(uint8_t algo) {
  _algoType = algo;
}


void BotDrive::setIMU(IMU_t imuData) {
  _imuData = imuData;
}

Drive_t BotDrive::getDrive() {
  return _driveData;
}


#endif

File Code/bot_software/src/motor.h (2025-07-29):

#ifndef MOTOR_H
#define MOTOR_H

#define MAX_PWM 4095

#include <Adafruit_PWMServoDriver.h>

struct MotorPWM_t {
  int16_t duty = 0;
  bool coast = false;
};

class Motor {
public:

  Motor(Adafruit_PWMServoDriver &pwm, uint16_t pinFwd, uint16_t pinRev, uint16_t pinLim, uint16_t pinEn);
  void begin();
  void setMotor(MotorPWM_t mot);
  void setCurrentLimit(uint16_t percent);

private:
  Adafruit_PWMServoDriver *_pwm;

  uint16_t _PIN_FWD;
  uint16_t _PIN_REV;
  uint16_t _PIN_ILIM;
  uint16_t _PIN_EN;

  int16_t lastDuty;
  uint32_t _lastSetTime;
  uint16_t _maxSlewRate = MAX_PWM * 10;  //pwms a second

  uint16_t _iLimitDuty = 4096;

  void _setPins(int16_t thisDuty);
};

Motor::Motor(Adafruit_PWMServoDriver &pwm, uint16_t pinFwd, uint16_t pinRev, uint16_t pinLim, uint16_t pinEn) {
  this->_pwm = &pwm;
  this->_PIN_FWD = pinFwd;
  this->_PIN_REV = pinRev;
  this->_PIN_ILIM = pinLim;
  this->_PIN_EN = pinEn;
}

void Motor::begin() {
  _pwm->setPin(_PIN_ILIM, _iLimitDuty);
  _pwm->setPin(_PIN_EN, 4096);
}

void Motor::setCurrentLimit(uint16_t percent) {
  if (percent > 100) return;
  _iLimitDuty = map(percent, 0, 100, 0, 4096);
  _pwm->setPin(_PIN_ILIM, _iLimitDuty);
}

void Motor::setMotor(MotorPWM_t mot) {
  int16_t thisDuty = mot.duty;
  thisDuty = constrain(thisDuty, -MAX_PWM, MAX_PWM);

  if (abs(thisDuty) > 0) {
    _pwm->setPin(_PIN_EN, 4096);
  }

  _setPins(thisDuty);

  if (mot.coast) {
    _pwm->setPin(_PIN_EN, 0);
  }
}

void Motor::_setPins(int16_t thisDuty) {
  uint32_t thisTime = millis();

  uint32_t timeDelta = thisTime - _lastSetTime;
  uint16_t dutySlew = _maxSlewRate / (1000 / timeDelta);

  if (abs(lastDuty - thisDuty) > dutySlew) {
    if (thisDuty > lastDuty) thisDuty = lastDuty + dutySlew;
    if (thisDuty < lastDuty) thisDuty = lastDuty - dutySlew;
  }

  thisDuty = constrain(thisDuty, -MAX_PWM, MAX_PWM);

  if (thisDuty > 0) {
    _pwm->setPin(_PIN_FWD, thisDuty);
    _pwm->setPin(_PIN_REV, 0);
  } else if (thisDuty < 0) {
    _pwm->setPin(_PIN_FWD, 0);
    _pwm->setPin(_PIN_REV, abs(thisDuty));
  } else {
    _pwm->setPin(_PIN_FWD, 0);
    _pwm->setPin(_PIN_REV, 0);
  }

  lastDuty = thisDuty;
  _lastSetTime = thisTime;
}

#endif

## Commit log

2025-02-23 documentation fix
    [botctrl.step]
2025-02-23 added credit for broken IMU filter
2025-07-29 updated to latest version
    [botctrl.kicad_pcb, botctrl.kicad_sch, drive.kicad_sch]
